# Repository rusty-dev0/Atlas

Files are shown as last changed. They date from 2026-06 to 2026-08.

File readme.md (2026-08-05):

# Colosseus
**A simplified robotics platform for students K-12.**

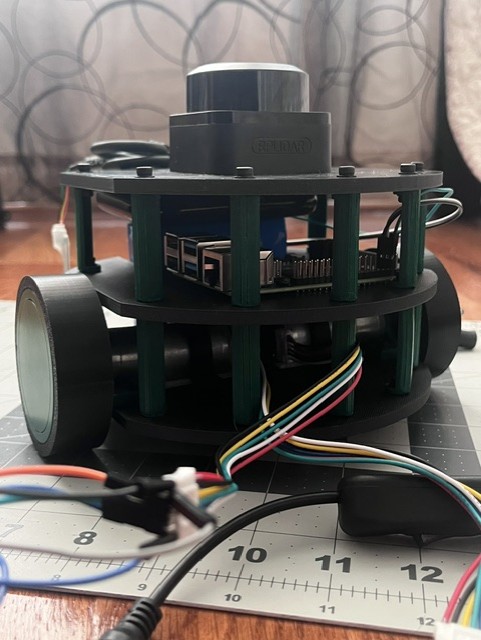
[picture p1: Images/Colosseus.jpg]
Atlas Assembly


*This project is still in a very early stage; take caution during the initial assembly. Be careful while operating the KineticBoard Leaf 0 because it can induce electric shock if not properly soldered.*

## What's Colosseus?
Colosseus is designed to be a two-wheeled robot that is easy to program and to learn. Its main feature is its stackable design, allowing more and more boards, often called "levels", to be added on top of it like pancakes. The demo version of Colosseus, which is featured in this repo, comes with a lidar as the main sensor on top.

## Repository Structure
The folders `Chassis` and `KineticBoard-Leaf` pertain to the M-CAD/E-CAD portions of this project, respectively. `KBLController` contains firmware for the KineticBoard Leaf microcontroller, which needs to be converted into a `.uf2` format by a `gcc-arm-none-eabi` cross-compiler. `Software` is an umbrella folder for the various software components for the Pi 4, but everything is neatly packaged into a Docker container for a quick and easy installation.

## What's Inside?
- **Raspberry Pi 4**: Essentially Atlas's "brain." It collects and processes information from various sensors and makes decisions based on them.
- **Lidar** (the main thing): It can detect nearby objects using what's essentially a rotating ToF sensor. The exact model is an RPLidar C1.
- **KineticBoard Leaf**: While the main Pi is busy handling computations and serving an interactive website, the KineticBoard Leaf is a custom microcontroller which spins the robot's motors based on commands from the Pi. The controller ensures that Colosseus moves exactly how it should using a PID loop.
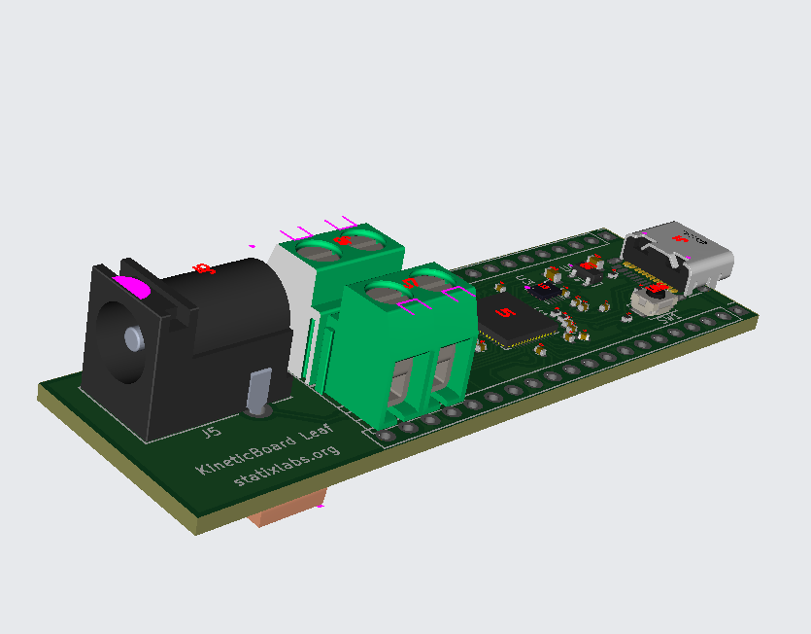
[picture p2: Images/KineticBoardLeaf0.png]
kineticBoard

- **WebUI**: The Pi hosts a web app using uvicorn to create WebSocket connections and allow users to easily interact with the robot. From here, students can "see" Colosseus' perspective. For instance, if one of the levels contains a camera, then an option to view the camera feed will be available. Similarly, if a lidar is connected, then there will be options to view the current point cloud readings from it, too.
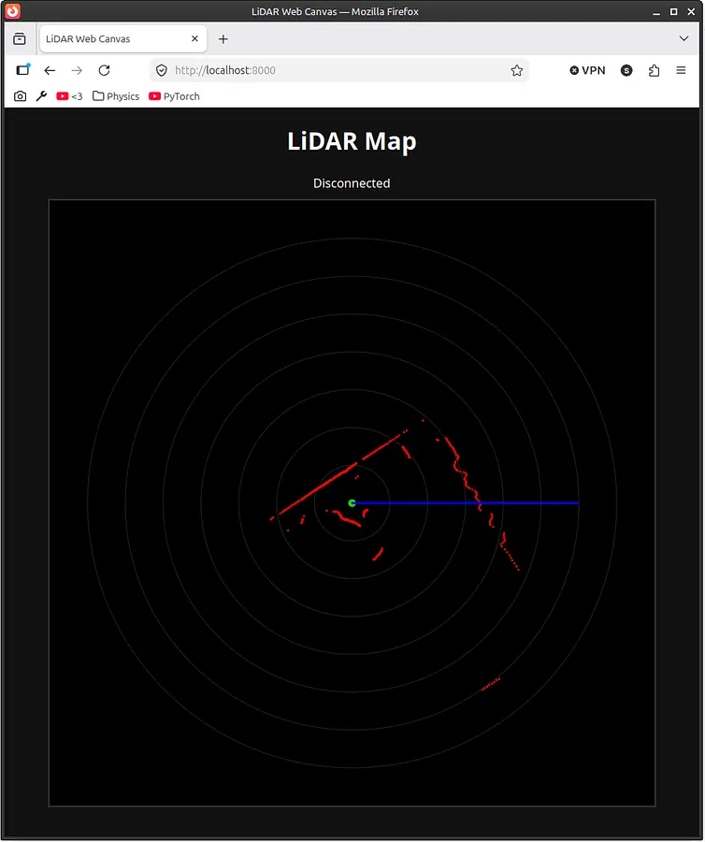
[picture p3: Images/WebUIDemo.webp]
webUI

## BOM
This is list of the parts that I need for this project. `BOM/lcsc.csv` contains the LCSC parts needed, and `BOM/tools.csv` lists the parts required for the rest of the robot from other online retailers like Amazon. Alternatively, I've added it to this README below:
### KineticBoard Assembly
| Designator | Footprint | Quantity | Value | LCSC Part # |
|---|---|---|---|---|
| C1, C10 | 0402 | 2 | 1uF | C52923 |
| C11, C12, C17, C2, C3, C4, C5, C6, C7, C8, C9 | 0402 | 11 | 0.1uF | C1525 |
| C13, C14, C18 | 0603 | 3 | 10uF | C96446 |
| C15, C16 | 0402 | 2 | 33pF | C1562 |
| C19, C21, C22, C24, C25 | 0402 | 5 | 100nF | C1525 |
| C20 | 0805 | 1 | 22uF | C1804 |
| C23 | CP_EIA-7343-31_Kemet-D | 1 | 100uF | C7469933 |
| D1, D2 | D_SMA | 2 | SS14 | C2480 |
| J1 | USB_C_Receptacle_HRO_TYPE-C-31-M-12 | 1 | USB_C_Receptacle_USB2.0_14P | C165948 |
| J2, J3 | PinHeader_1x20_P2.54mm_Vertical | 2 | Conn_01x20 | |
| J5 | BarrelJack_CUI_PJ-102AH_Horizontal | 1 | Barrel_Jack_Switch | C3096093 |
| J6 | TerminalBlock_MaiXu_MX126-5.0-02P_1x02_P5.00mm | 1 | Motor A | C5188434 |
| J7 | TerminalBlock_MaiXu_MX126-5.0-02P_1x02_P5.00mm | 1 | Motor B | C5188434 |
| L1 | 0805 | 1 | 4.7uH | C48945383 |
| R1, R2 | 0402 | 2 | 5.1K | C25905 |
| R3, R4 | 0402 | 2 | 27 | C25156 |
| R5, R7 | 0402 | 2 | 1K | C11702 |
| R6 | 0402 | 1 | 10K | C25744 |
| SW1 | SW_Push_SPST_NO_Alps_SKRK | 1 | SW_Push | C115357 |
| U1 | QFN-56-1EP_7x7mm_P0.4mm_EP3.2x3.2mm | 1 | RP2040 | C2040 |
| U3 | Winbond_USON-8-1EP_3x2mm_P0.5mm_EP0.2x1.6mm | 1 | W25Q16JVZPIQ TR | C2843335 |
| U4 | TSOT-23-6 | 1 | AP63203WU | C780769 |
| U5 | SSOP-24_5.3x8.2mm_P0.65mm | 1 | TB6612FNG | C88224 |
| U6 | SOT-23 | 1 | MCP1700x-330xxTT | C39051 |
| Y1 | Crystal_SMD_3225-4Pin_3.2x2.5mm | 1 | 12 MHz | C9002 |
### Reflow Soldering Station
- [Solder Paste](https://www.amazon.com/gp/product/B08KR7W7SQ/ref=ox_sc_act_title_1?smid=A2GPLZGUK8NBW5&psc=1) ~$13
- [Solder Flux](https://www.amazon.com/gp/product/B0D2DC28XF/ref=ox_sc_act_title_2?smid=A3FX7C4A9P37IQ&psc=1) ~$10
- [Hot Plate](https://www.amazon.com/gp/product/B0G443BG4X/ref=ox_sc_act_title_3?smid=AWT2BCWPY562U&psc=1) ~$30
- [Extra Precise Tweezers](https://www.amazon.com/gp/product/B0D6RRJNRQ/ref=ox_sc_act_title_4?smid=ALGTK11E8KWSQ&psc=1) ~$14
### Robot
- [2pcs Motors w/ Encoders](https://www.amazon.com/XiaoR-Motor-Encoder-100RPM-Ratio/dp/B0FFMK7CLT) ~$31
- [Li-Ion Battery Pack](https://www.amazon.com/Zenshynix-Rechargeable-Lithium-Ion-High-Capacity-Telescope/dp/B0G1SW4JHR) ~$19
- [Screw Assortment Kit](https://www.amazon.com/HanTof-Countersunk-Assortment-Phillips-Threaded/dp/B0FF4RFTN6/ref=sr_1_9) ~$8
- Raspberry Pi 4B+ 4GB (I already own this)
- 32GB MicroSD Card (I already own this)
- RPLidar C1 (I already own this)
- Chassis Parts (I have cheap access to a 3D printer at my local library)

### Totals
- Cost of the linked parts: $125
- JLCPCB PCB + Stencil Order: $30
- LCSC Parts: $22

**Total Cost: ~$177**

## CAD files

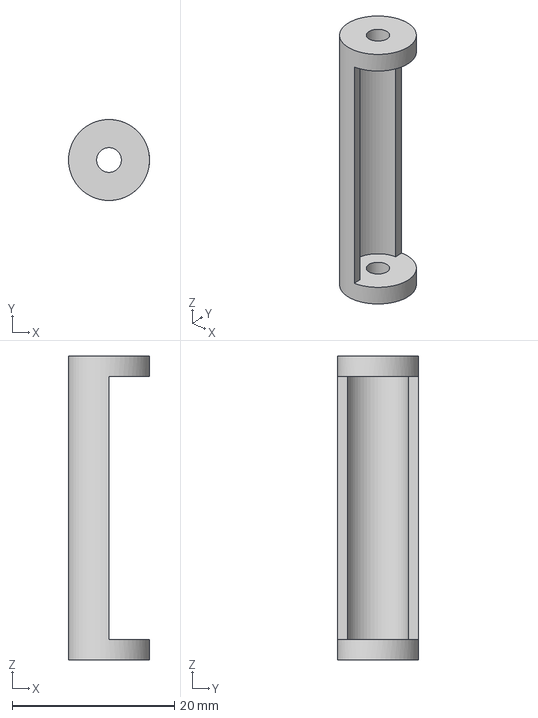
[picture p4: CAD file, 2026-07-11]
chassis/step/Support.step
10.0 x 10.0 x 37.5 mm

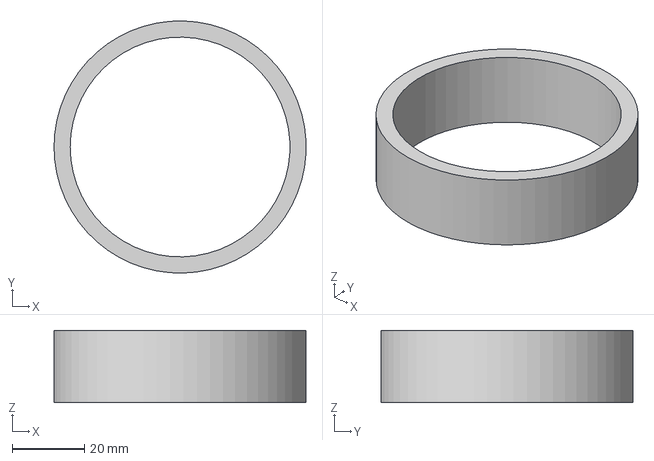
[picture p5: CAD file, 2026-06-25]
chassis/step/Tire.step
70.0 x 70.0 x 20.0 mm

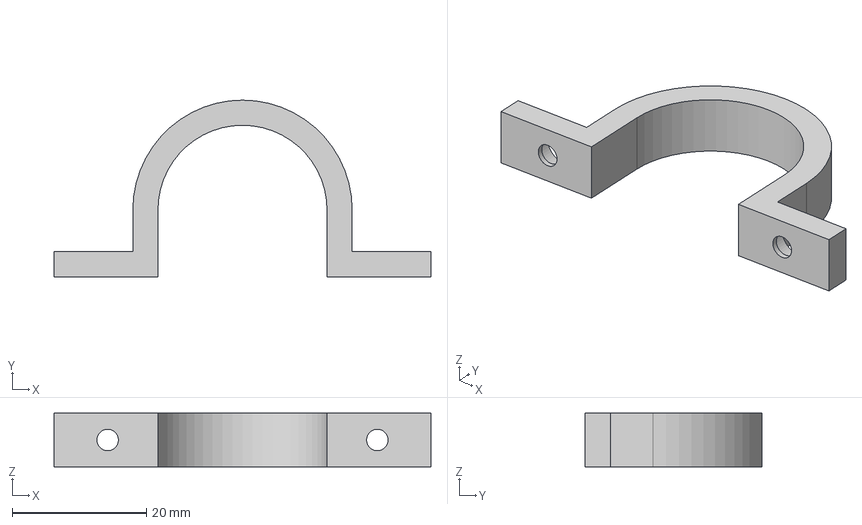
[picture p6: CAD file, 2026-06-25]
chassis/step/Saddle Clamp.step
56.2 x 26.4 x 8.00 mm

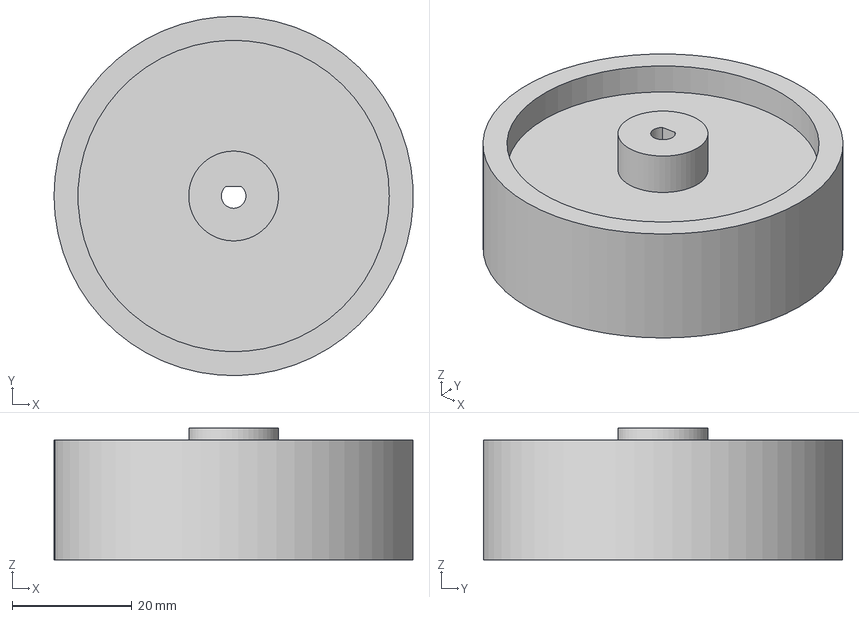
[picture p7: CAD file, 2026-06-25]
chassis/step/Wheel.step
60.0 x 60.0 x 22.0 mm

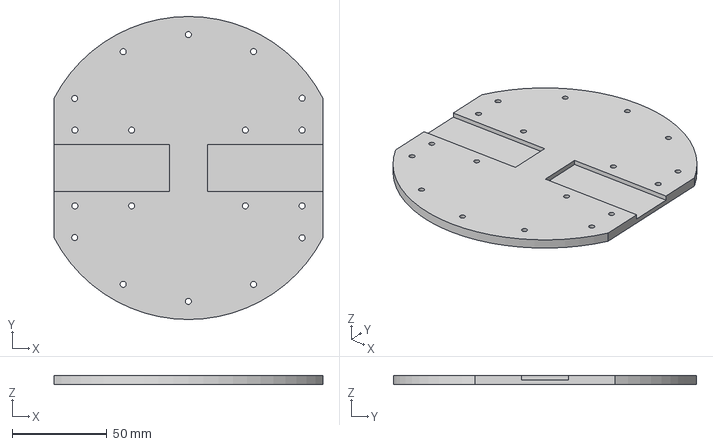
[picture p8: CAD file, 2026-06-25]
chassis/step/Chasis.step
142.0 x 160.0 x 5.00 mm

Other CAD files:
chassis/step/Middle Chasis.step
chassis/step/Upper Chasis.step
chassis/fusion/Chasis.f3d
chassis/fusion/Middle Chasis.f3d
chassis/fusion/Saddle Clamp.f3d
chassis/fusion/Support.f3d
chassis/fusion/Tire.f3d
chassis/fusion/Upper Chasis.f3d
chassis/fusion/Wheel.f3d

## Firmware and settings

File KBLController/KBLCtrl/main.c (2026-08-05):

#include "driver.h"
#include "board.h"
#include "hardware/gpio.h"
#include "hardware/irq.h"

// encoder state shared between ISR and main
volatile int encoder_count = 0;
volatile bool last_state_a = false;
volatile bool last_state_b = false;
volatile bool encoder_initialized = false;

void update_encoder_count(uint gpio, uint32_t events) {
    bool state_a = gpio_get(AENC1);
    bool state_b = gpio_get(AENC2);

    if (!encoder_initialized) {
        last_state_a = state_a;
        last_state_b = state_b;
        encoder_initialized = true;
        return;
    }

    if (state_a != last_state_a || state_b != last_state_b) {
        if (state_a == state_b) {
            encoder_count++;
        } else {
            encoder_count--;
        }
    }

    last_state_a = state_a;
    last_state_b = state_b;
}

int main() {
    stdio_init_all();

    struct motor *m1 = motor_init(AIN1, AIN2, APWM);
    struct motor *m2 = motor_init(BIN1, BIN2, BPWM);

    // // set up encoder pins
    // gpio_init(AENC1);
    // gpio_init(AENC2);

    // gpio_set_dir(AENC1, GPIO_IN);
    // gpio_set_dir(AENC2, GPIO_IN);

    // gpio_pull_up(AENC1);
    // gpio_pull_up(AENC2);

    // // read and store initial encoder state before enabling IRQs
    // last_state_a = gpio_get(AENC1);
    // last_state_b = gpio_get(AENC2);
    // encoder_initialized = true;

    // gpio_set_irq_enabled_with_callback(AENC1, GPIO_IRQ_EDGE_RISE | GPIO_IRQ_EDGE_FALL, true, update_encoder_count);
    // gpio_set_irq_enabled_with_callback(AENC2, GPIO_IRQ_EDGE_RISE | GPIO_IRQ_EDGE_FALL, true, update_encoder_count);

    if (!m1 || !m2) {
        return 1;
    }

    // this results in forward movement because I swapped the polarity on the second motor
    motor_spin(m1, 0.5f, MOTOR_CW);
    motor_spin(m2, 0.5f, MOTOR_CW);

    

    while (true) {
        // printf("Encoder Count: %d\n", encoder_count);
        // sleep_ms(500);
        tight_loop_contents();
    }

    motor_deinit(m1);
    motor_deinit(m2);

    return 0;
}

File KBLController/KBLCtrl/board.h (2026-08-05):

// for testing only
#define PIN_A 0

// first motor
#define AIN1 2
#define AIN2 3
#define APWM 4

// encoders for first motor
#define AENC1 8
#define AENC2 9

// second motor
#define BIN1 5
#define BIN2 6
#define BPWM 7

// robot-related macros
#define COL_WHEEL_DIAMETER 70.0f

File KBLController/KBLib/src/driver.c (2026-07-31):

#include <stdlib.h>
#include "driver.h"

void gpio_test() {
    stdio_init_all();

#ifdef PIN_A
    gpio_init(PIN_A);
    gpio_set_dir(PIN_A, GPIO_OUT);
    
    bool state = 0;

    while (true) {
        state = !state;
        gpio_put(PIN_A, state);
        sleep_ms(1000);
    }
#endif
}

struct pwm *motor_pwm_init(uint pin) {
    gpio_set_function(pin, GPIO_FUNC_PWM);
    uint slice_num = pwm_gpio_to_slice_num(pin);
    uint channel = pwm_gpio_to_channel(pin);
    pwm_set_enabled(slice_num, true);
    pwm_set_wrap(slice_num, WRAP);
    struct pwm *p = malloc(sizeof(*p));
    if (!p) return NULL;
    p->slice_num = slice_num;
    p->channel = channel;
    return p;
}

void motor_pwm_set_speed(struct pwm *pwm, float speed) {
    if (!pwm) return;
    if (speed < 0.0f) {
        speed = 0.0f;
    } else if (speed > 1.0f) {
        speed = 1.0f;
    }
    uint level = (uint)(speed * WRAP);
    pwm_set_chan_level(pwm->slice_num, pwm->channel, level);
}

void motor_pwm_deinit(struct pwm *pwm) {
    if (!pwm) return;
    pwm_set_enabled(pwm->slice_num, false);
    free(pwm);
}

struct motor *motor_init(uint in1, uint in2, uint pwm_pin) {
    gpio_init(in1);
    gpio_init(in2);
    gpio_set_dir(in1, GPIO_OUT);
    gpio_set_dir(in2, GPIO_OUT);
    struct pwm *speed = motor_pwm_init(pwm_pin);
    struct motor *m = malloc(sizeof(*m));
    if (!m || !speed) {
        if (speed) {
            motor_pwm_deinit(speed);
        }
        else if (m) {
            free(m);
        }
        return NULL;
    }
    m->in1 = in1;
    m->in2 = in2;
    m->speed = NULL;

    m->speed = speed;
    return m;
}

void motor_set_direction(struct motor *m, enum motor_direction dir) {
    if (!m) return;
    switch (dir) {
        case MOTOR_CW:
            gpio_put(m->in1, GPIO_HIGH);
            gpio_put(m->in2, GPIO_LOW);
            break;
        case MOTOR_CCW:
            gpio_put(m->in1, GPIO_LOW);
            gpio_put(m->in2, GPIO_HIGH);
            break;
        case MOTOR_STOP:
            gpio_put(m->in1, GPIO_LOW);
            gpio_put(m->in2, GPIO_LOW);
            break;
        case MOTOR_BRAKE:
            gpio_put(m->in1, GPIO_HIGH);
            gpio_put(m->in2, GPIO_HIGH);
            break;
    }
}

void motor_spin(struct motor *m, float speed, enum motor_direction dir) {
    if (!m) return;
    motor_set_direction(m, dir);
    motor_pwm_set_speed(m->speed, speed);
}

void motor_deinit(struct motor *m) {
    if (!m) return;
    motor_pwm_deinit(m->speed);
    gpio_deinit(m->in1);
    gpio_deinit(m->in2);
    free(m);
}

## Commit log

2026-06-20 add web app that displays lidar's polar point cloud data
2026-06-21 create listener for the kineticBoard driver
2026-06-24 add support for second motor and turning
2026-06-25 added fusion files
    [Chasis.f3d, Chasis.step, Middle Chasis.f3d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]
